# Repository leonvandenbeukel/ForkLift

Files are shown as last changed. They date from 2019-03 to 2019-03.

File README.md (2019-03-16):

# ForkLift

### Schema

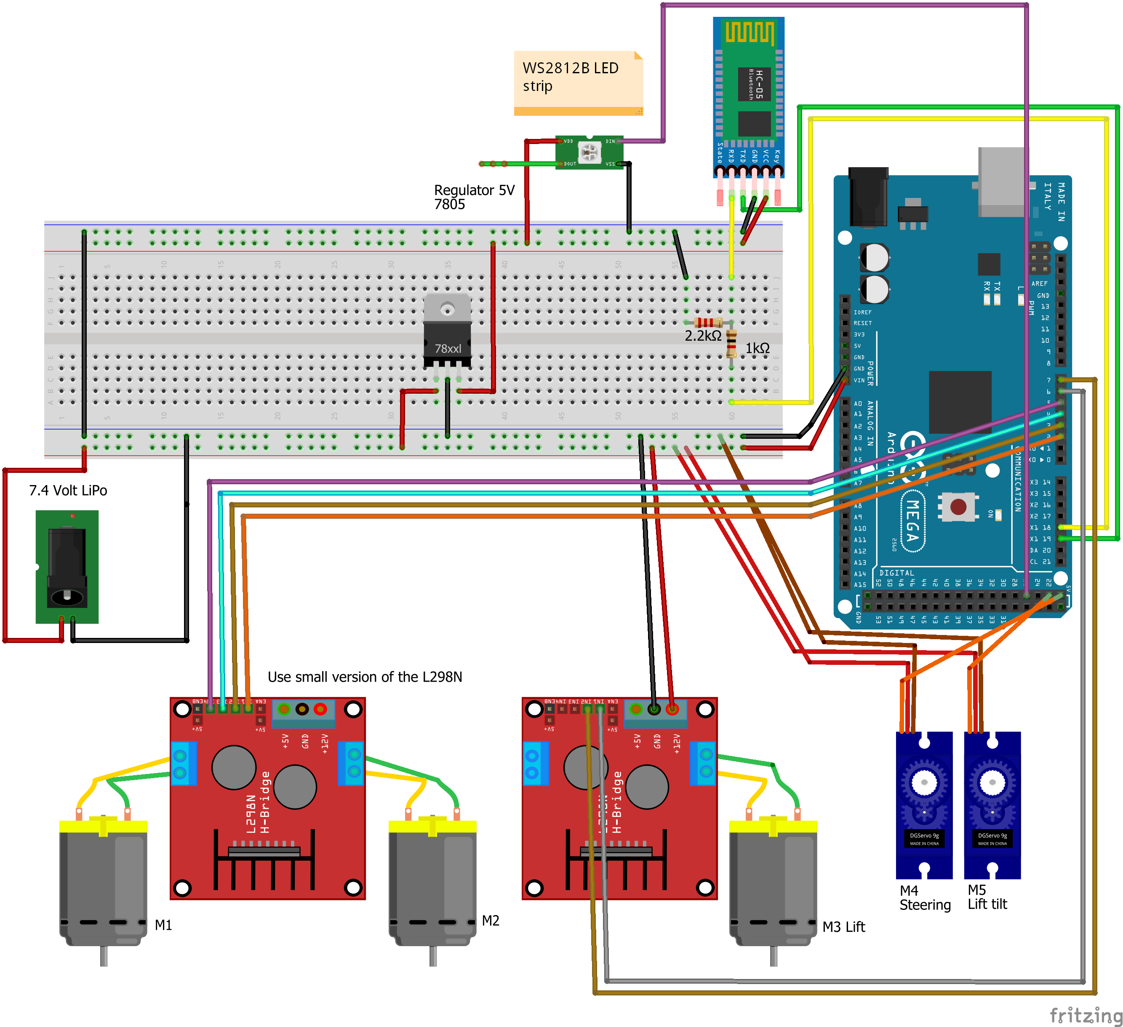
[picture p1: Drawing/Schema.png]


### Parts list (just Google on the name to find a link where to buy)

| Components                              			    |
| -------------                          			      |
| Arduino Mega                           			      |
| LED strip WS2812B 8 RGB LED's		 	                |
| 3x Smart Car Robot Motor (yellow)           		  |
| 4x Smart Car Robot Wheel (yellow)                 |
| 2x Small Servo SG90                               |
| 2x Small H-Bridge L298N                           |
| Bluetooth module: HC-05                 			    |
| 3x 11x4 mm Bearing  	                            |
| 7.4V LiPo Battery 								                |
| 15x15mm Square aluminium tube (2x20cm, 2x14cm)    |
| 10mm Round aluminium tube (2x20cm)       			    |
| GT2 Belt approx. 40cm                             |
| Plywood 4mm                                       |
| M3 screws and nuts                                |
| Small amount of several other nuts and bolts      |

### YouTube video

<a href="https://youtu.be/_YNgo8A7p8A" target="_blank">Click to view: Arduino Forklift</a>

### Android App

The Xamarin Android App can be found on:

https://github.com/leonvandenbeukel/ForkLift-App

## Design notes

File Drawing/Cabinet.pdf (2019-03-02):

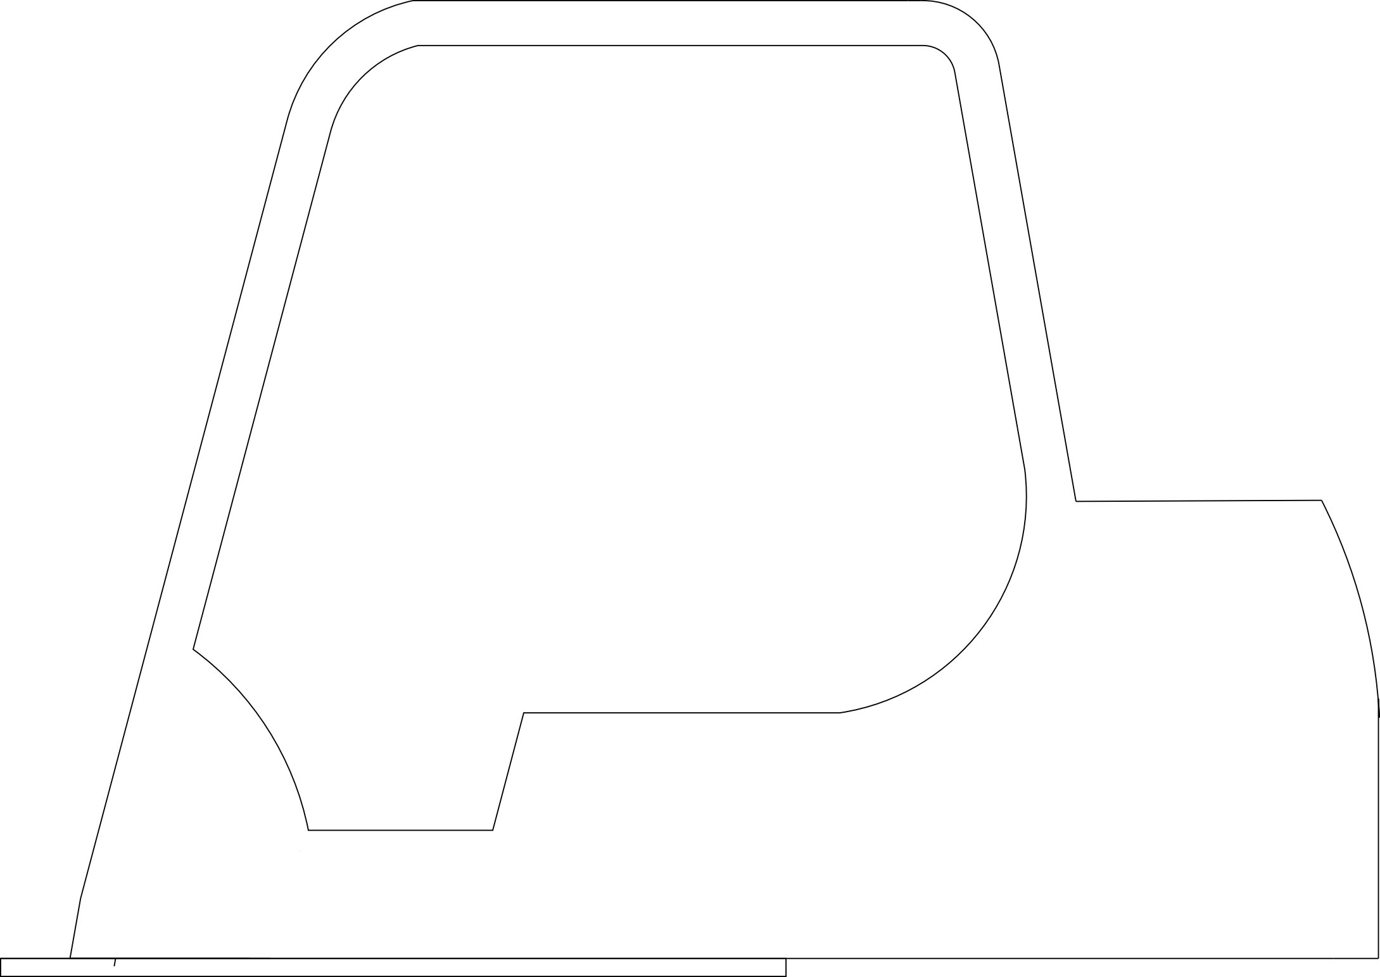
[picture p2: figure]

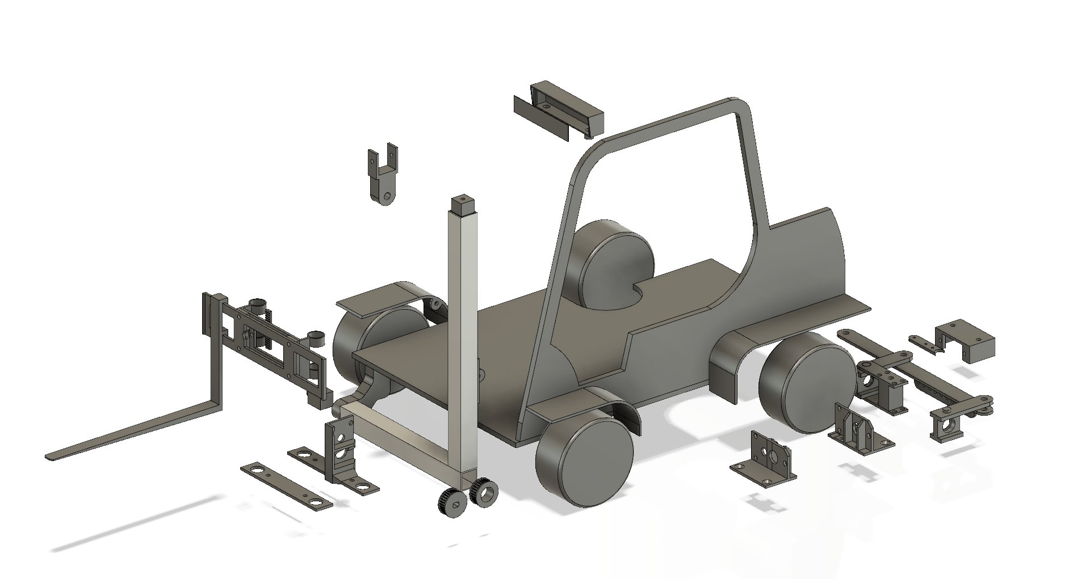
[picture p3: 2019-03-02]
Drawing/CAD.png

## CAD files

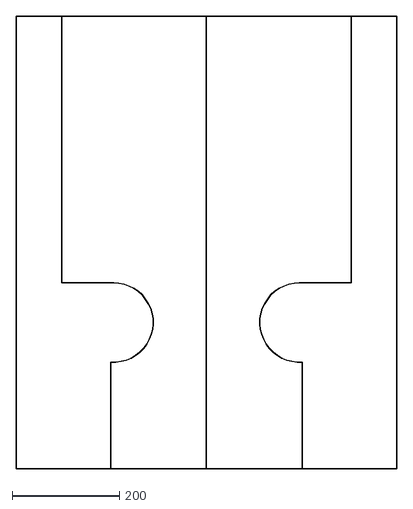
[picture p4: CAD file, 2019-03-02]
Drawing/Base.dxf
708.7 x 841.9

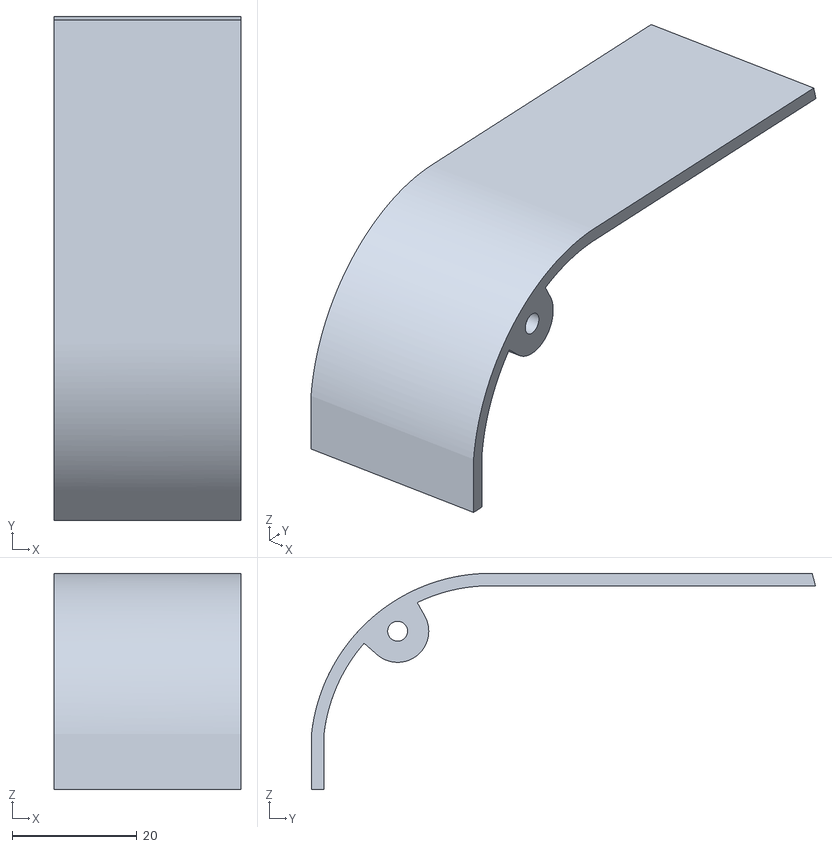
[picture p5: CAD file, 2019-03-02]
STL/Wheel-Cap-Front-Left.stl
30.0 x 80.9 x 34.7

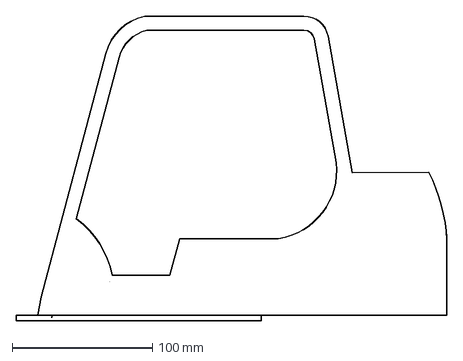
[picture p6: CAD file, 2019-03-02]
Drawing/Cabinet.dxf
307.2 x 217.4 mm

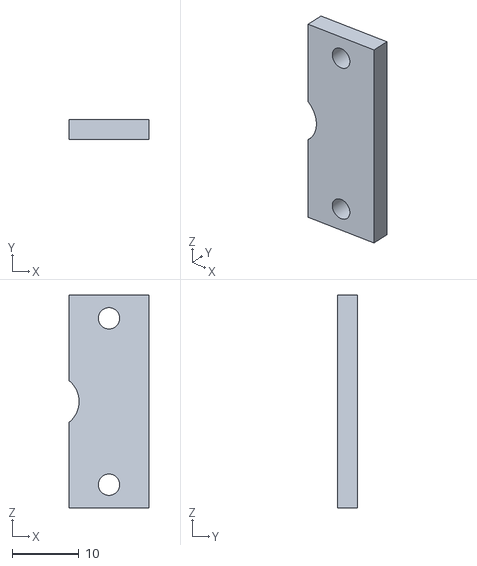
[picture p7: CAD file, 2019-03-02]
STL/Fork-Attachment-Spacer.stl
12.0 x 3.00 x 32.0

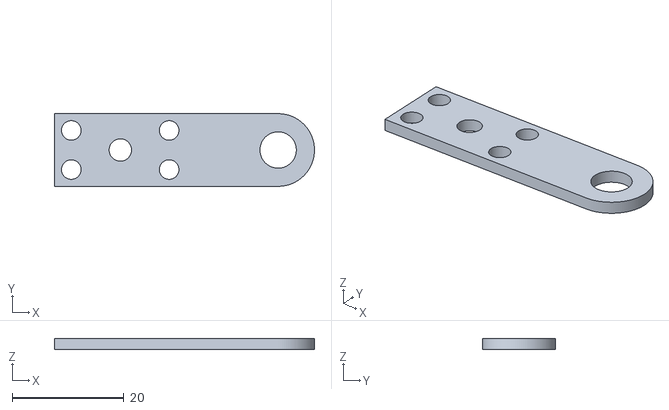
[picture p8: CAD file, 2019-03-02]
STL/Steering-Bottom.stl
46.5 x 13.0 x 2.00

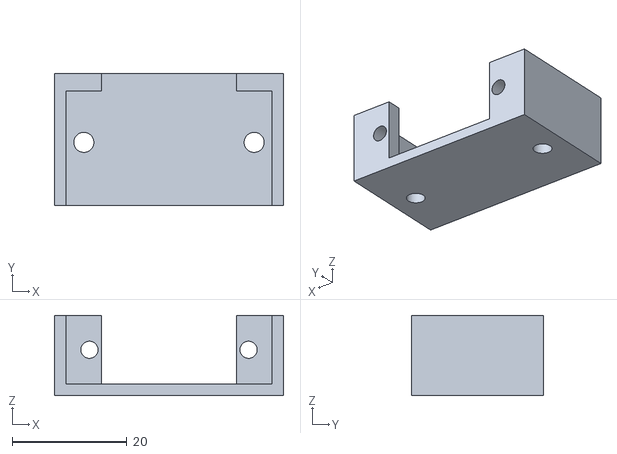
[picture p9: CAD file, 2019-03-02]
STL/Servo-Holder.stl
40.0 x 23.0 x 14.0

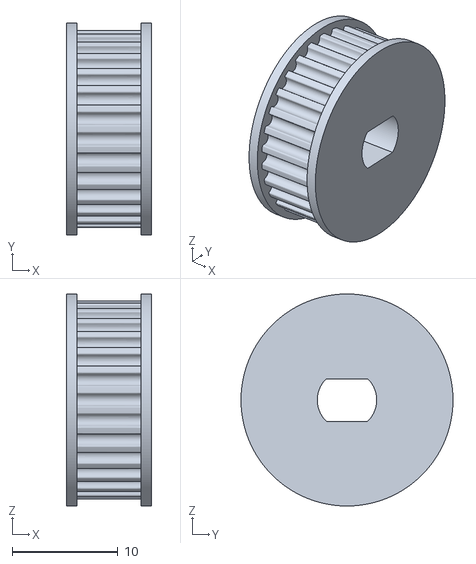
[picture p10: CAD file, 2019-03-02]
STL/Gear1.stl
8.00 x 20.0 x 20.0

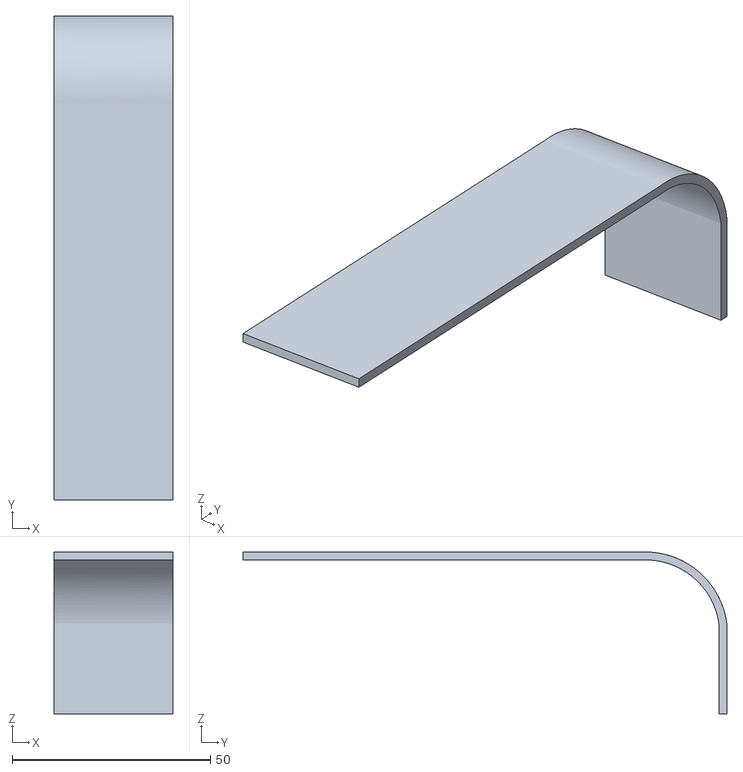
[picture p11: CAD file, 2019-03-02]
STL/Wheel-Cap-Back.stl
30.0 x 122.0 x 40.9

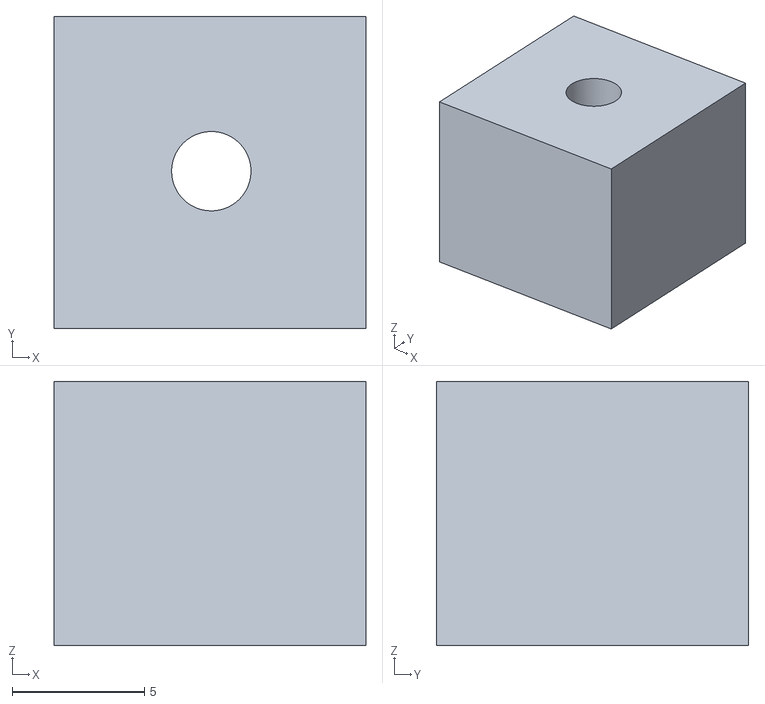
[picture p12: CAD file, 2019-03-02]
STL/Aluminium-Connector1.stl
11.8 x 11.8 x 10.0

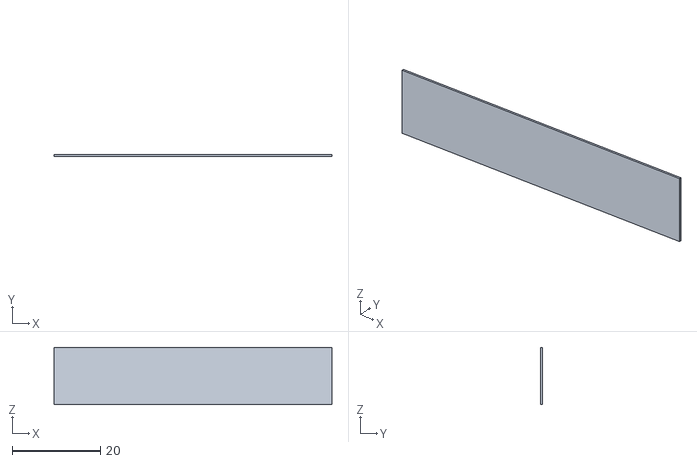
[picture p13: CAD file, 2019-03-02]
STL/Head-Light-Front.stl
63.0 x 0.4 x 13.0

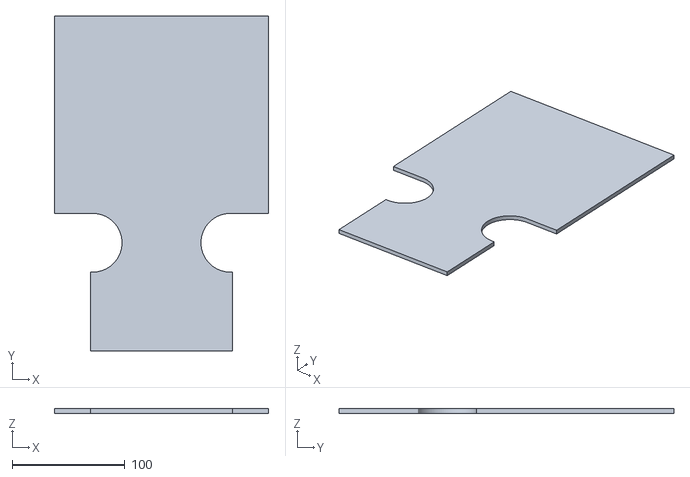
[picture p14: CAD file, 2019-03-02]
STL/Base.stl
190.0 x 297.0 x 4.00

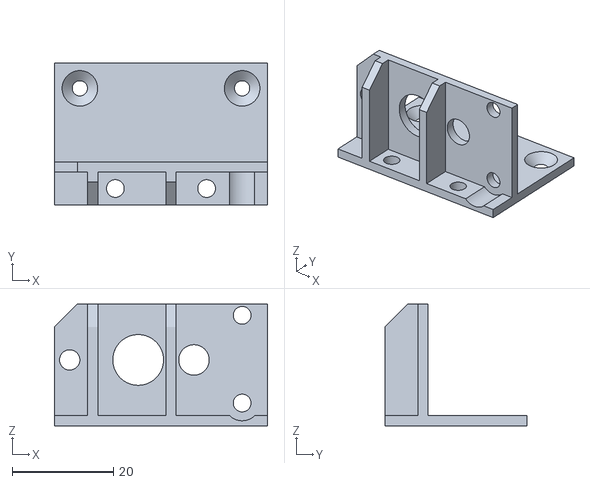
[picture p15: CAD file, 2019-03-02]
STL/Motor-Mount2.stl
42.0 x 28.0 x 24.0

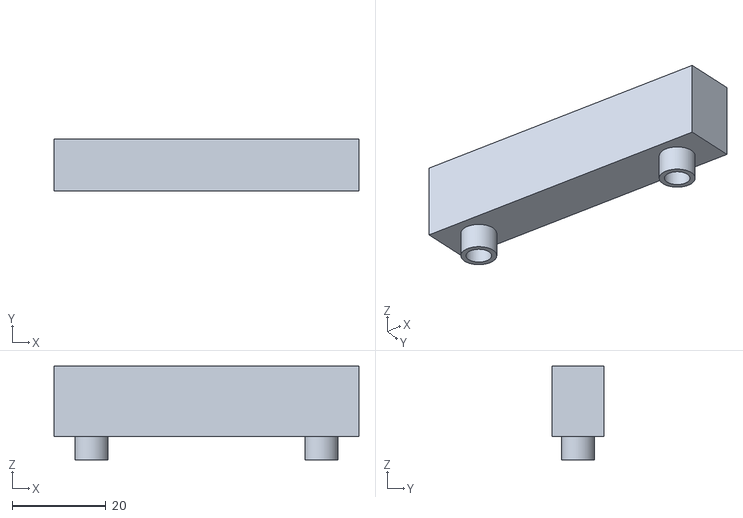
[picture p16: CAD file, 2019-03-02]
STL/Head-Light-Inner.stl
65.0 x 11.0 x 20.0

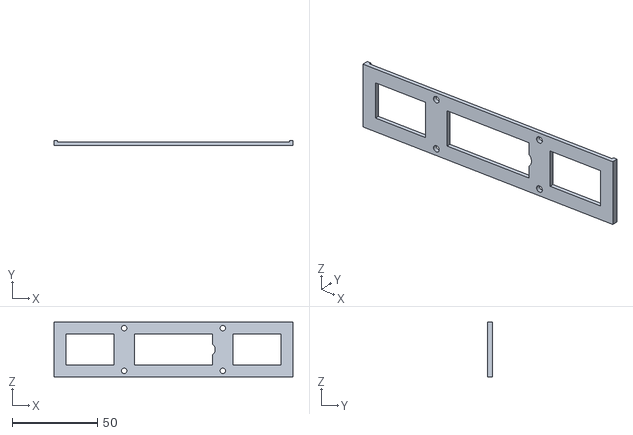
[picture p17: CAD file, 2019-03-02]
STL/Fork-Attachment.stl
140.0 x 3.00 x 32.0

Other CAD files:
STL/Wheel-Cap-Front-Right.stl
STL/Gear2.stl
STL/Motor-Mount1.stl
STL/Motor-Mount-Lift.stl
STL/Aluminium-Connector2.stl
STL/Belt-Holder.stl
STL/Fork.stl
STL/Gear-Mount-Top.stl
STL/Head-Light-Cover.stl
STL/Liftmount.stl
STL/Servo-Arm-Extender.stl
STL/Servo-Connector.stl
STL/Slider-Top-Holder.stl
STL/Slider.stl
STL/Steering-Handle-Spacer.stl
STL/Steering-Handle.stl
STL/Steering-Top.stl
STL/Wheel-Attachment.stl

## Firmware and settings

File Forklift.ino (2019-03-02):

/*
 * MIT License
 * 
 * Copyright (c) 2019 Leon van den Beukel
 * 
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
 * Source: 
 * https://github.com/leonvandenbeukel/ForkLift * 
 * 
 * Use an Arduino Mega 2560 because: 
 *  - Cannot use SoftwareSerial for the Bluetooth module because this will mess up the internal timers when using the Servo lib and causing servo jitter
 *  - At least 6 PWM pins are needed for the motors, the Servo lib disables PWM on pins 9 & 10  
 *    
 */

#include <Servo.h>
#include <FastLED.h>

Servo servoSteering;        
Servo servoLift;    

// Calibrate these servos values
int servoMaxLeft = 30;                                // Steering value when at the lowest position
int servoMaxRight = 145;                              // Steering value when at the highest position
int servoCenter = (servoMaxRight - servoMaxLeft)/2;   // Steering center position
int servoLiftCenter = 85;                             // Vertical lift center position
int servoLiftCenterMax = 155;                         // Vertical lift maximum position forward:  85 + 70
int servoLiftCenterMin = 35;                          // Vertical lift minimum position backward: 85 - 50

#define servoPin 22          
#define servoLiftPin 24

#define NUM_LEDS 8     
#define DATA_PIN 26
CRGB LEDs[NUM_LEDS];

String btBuffer;
 
#define Ain1 2
#define Ain2 3

#define Bin1 4
#define Bin2 5

#define Ain1_lift 6
#define Ain2_lift 7

void setup() {

  FastLED.delay(3000);
  FastLED.addLeds<WS2812B, DATA_PIN, GRB>(LEDs, NUM_LEDS);
  
  servoSteering.attach(servoPin);     
  servoLift.attach(servoLiftPin);

  Serial.begin(57600);          // Debug
  Serial1.begin(9600);          // Bluetooth

  pinMode(Ain1, OUTPUT);        // A in1
  pinMode(Ain2, OUTPUT);        // A in2
  pinMode(Bin1, OUTPUT);        // B in1
  pinMode(Bin2, OUTPUT);        // B in2
  pinMode(Ain1_lift, OUTPUT);   // Lift motor
  pinMode(Ain2_lift, OUTPUT);   // Lift motor

  ledStartup();  

  analogWrite(Ain1,0);
  analogWrite(Ain2,0);
  analogWrite(Bin1,0);
  analogWrite(Bin2,0);
  analogWrite(Ain1_lift, 0);
  analogWrite(Ain2_lift, 0);
  
  servoSteering.write(servoCenter); 
  servoLift.write(servoLiftCenterMin);  
}

void loop() {

  if (Serial1.available())
  {
    char received = Serial1.read();
    btBuffer += received; 
    if (received == '|')
    {
        Serial.println(btBuffer);
        processCommand();
        btBuffer = "";
    }
  }    
}

void processCommand() {
  char separator = ',';
  int percW = getValue(btBuffer, separator, 0).toInt();
  int percH = getValue(btBuffer, separator, 1).toInt();
  int liftPos = getValue(btBuffer, separator, 2).toInt();
  int liftVerticalPos = getValue(btBuffer, separator, 3).toInt();
  int lightOn = getValue(btBuffer, separator, 4).toInt();
  int valServo = map(percW, 100, 0, servoMaxLeft, servoMaxRight);   // Switch the values 100 and 0 to reverse direction
  int valLiftServo = map(liftVerticalPos, 100, 0, servoLiftCenterMin, servoLiftCenterMax); 
  int spdMotor = 0;

  Serial.print("W: ");
  Serial.print(percW);
  Serial.print(", H: ");  
  Serial.print(percH);
  Serial.print(", Servo: ");
  Serial.print(valServo);
  Serial.print(", Lift position: ");
  Serial.print(liftPos);  
  Serial.print(", Vertical raw: ");
  Serial.print(liftVerticalPos);
  Serial.print(", Vertical calculated: ");
  Serial.print(valLiftServo);

  // Forward/Backward
  if (percH < 50) {
    spdMotor = map(percH, 50, 0, 50, 255);
    Serial.print(", Motor Forward: ");
    Serial.print(spdMotor);
    motorForward(spdMotor);
  } else if (percH > 50) {
    spdMotor = map(percH, 50, 100, 50, 255);
    Serial.print(", Motor Backwards: ");
    Serial.print(spdMotor);
    motorBackward(spdMotor);
  } else if (percH == 50) {
    stopMoving();
  } 

  // Lift Up/Down
  if (liftPos == 0) {
    analogWrite(Ain1_lift, 0);
    analogWrite(Ain2_lift, 0);    
  } else if (liftPos > 0) {
    int perc2val = map(liftPos, 0, 100, 0, 255);
    analogWrite(Ain1_lift, perc2val);
    analogWrite(Ain2_lift, 0);    
  } else if (liftPos < 0) {
    int perc2val = map(liftPos, 0, -100, 0, 255);
    analogWrite(Ain1_lift, 0);
    analogWrite(Ain2_lift, perc2val);    
  }

  // Lift vertical position Forward/Backward
  servoLift.write(valLiftServo);

  // Steering Left/Right
  servoSteering.write(valServo);

  if (lightOn == 1) {
    ledToggle(CRGB::White);
  } else {
    ledToggle(CRGB::Black);
  }

  Serial.println();
  delay(60);  
}

// Switch the names of the functions motorBackward and motorForward to reverse direction
void motorBackward(int spd) {  
  analogWrite(Ain1,spd);  
  analogWrite(Ain2,0);
  analogWrite(Bin2,spd);
  analogWrite(Bin1,0);
}

// Switch the names of the functions motorBackward and motorForward to reverse direction
void motorForward(int spd) {
  analogWrite(Ain1,0);
  analogWrite(Ain2,spd);
  analogWrite(Bin2,0);
  analogWrite(Bin1,spd);
}

void stopMoving() {
  analogWrite(Ain1,0);
  analogWrite(Ain2,0);
  analogWrite(Bin2,0);
  analogWrite(Bin1,0);
}

void ledStartup() {

  int dly = 700;
  LEDs[0] = CRGB::Red;
  LEDs[7] = CRGB::Red;
  FastLED.show();  
  delay(dly);
  ledToggle(CRGB::Black);
  LEDs[1] = CRGB::Red;
  LEDs[6] = CRGB::Red;
  FastLED.show();  
  delay(dly);
  ledToggle(CRGB::Black);
  LEDs[2] = CRGB::Red;
  LEDs[5] = CRGB::Red;
  FastLED.show();  
  delay(dly);
  ledToggle(CRGB::Black);
  LEDs[3] = CRGB::Red;
  LEDs[4] = CRGB::Red;
  FastLED.show();  
  delay(dly);

  ledToggle(CRGB::Black);
}

void ledToggle(CRGB color) {
   for (int i=0; i<NUM_LEDS; i++){
    LEDs[i] = color;
  }
  FastLED.show();  
}

String getValue(String data, char separator, int index) {
  int found = 0;
  int strIndex[] = {0, -1};
  int maxIndex = data.length()-1;

  for(int i=0; i<=maxIndex && found<=index; i++){
    if(data.charAt(i)==separator || i==maxIndex){
        found++;
        strIndex[0] = strIndex[1]+1;
        strIndex[1] = (i == maxIndex) ? i+1 : i;
    }
  }
  return found>index ? data.substring(strIndex[0], strIndex[1]) : "";
}

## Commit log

2019-03-01 Cleanup code and modified lift to use PWM values
2019-03-02 Added LED's
2019-03-02 Added STL files and drawing files
    [Aluminium-Connector1.stl, Aluminium-Connector2.stl, Base.dxf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]
2019-03-03 Added schema
    [Schema.fzz]
